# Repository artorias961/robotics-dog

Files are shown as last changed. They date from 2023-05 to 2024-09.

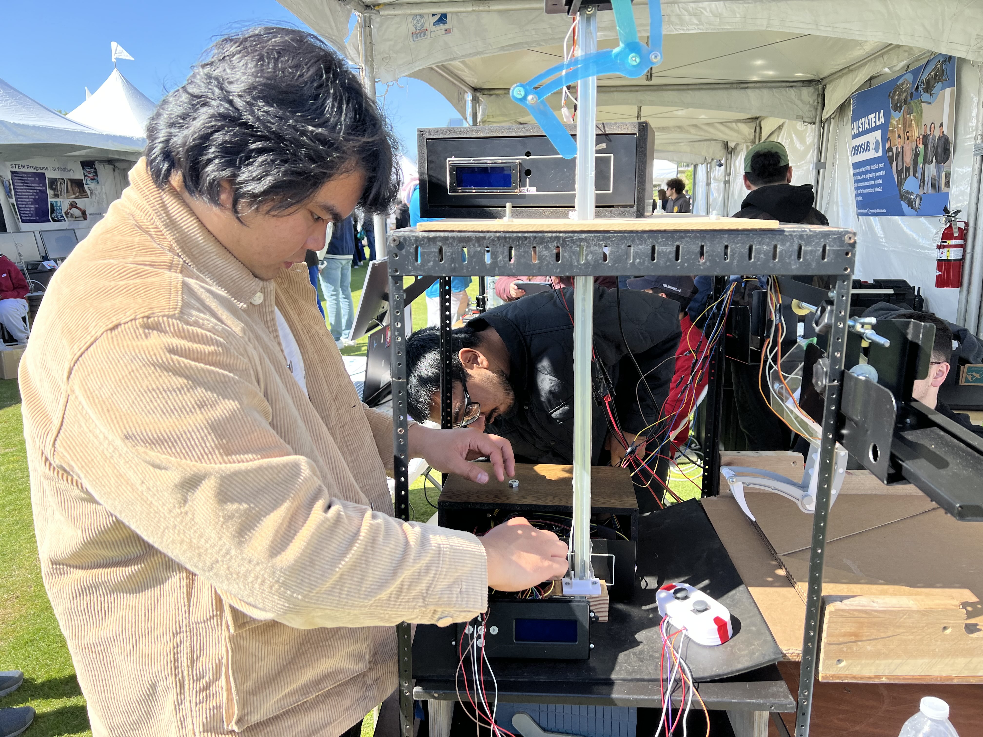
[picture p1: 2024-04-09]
events_photos/Spring_2024_Maker_Faire_Downtown_LA/IMG_5998.jpg

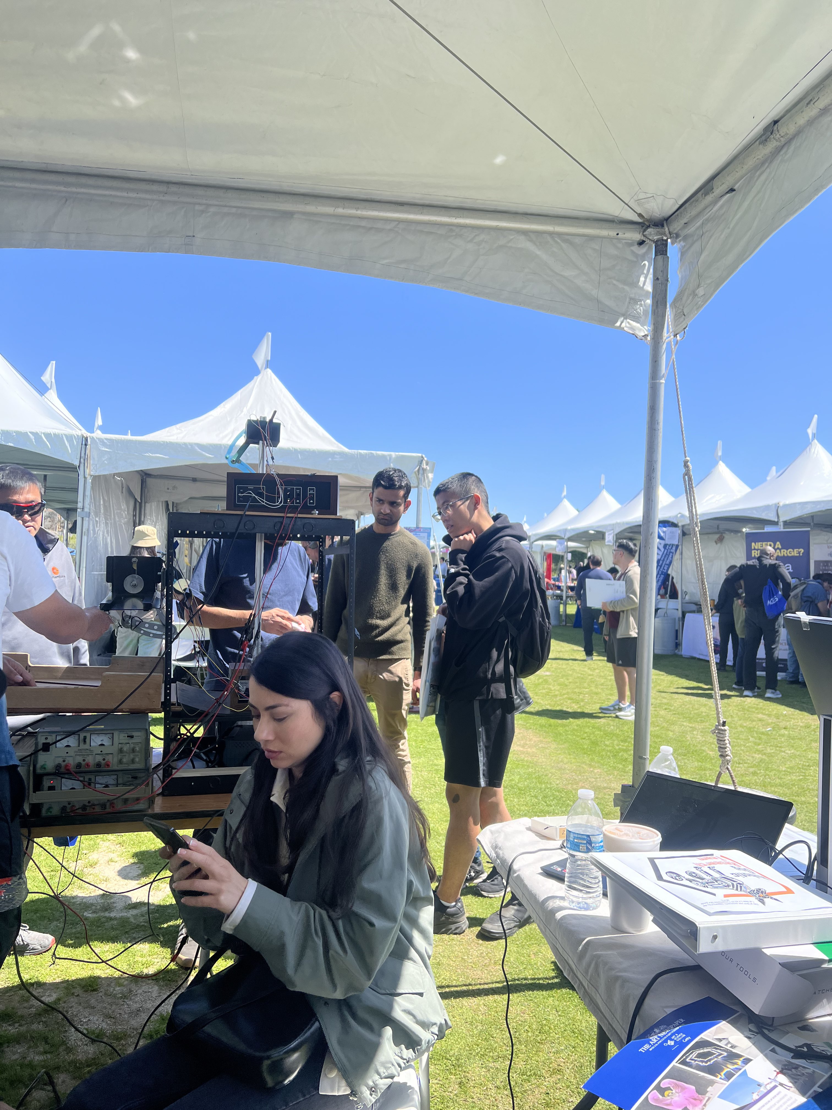
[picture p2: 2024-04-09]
events_photos/Spring_2024_Maker_Faire_Downtown_LA/IMG_3934.jpg

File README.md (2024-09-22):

# Idea of the Project

This project aims to develop a guided tour robot designed to assist individuals with disabilities in navigating the California State University, Los Angeles campus. The robot will utilize detailed floor plans of campus buildings and follow a pre-set route. It will be equipped with advanced computer vision technology to detect and avoid obstacles, enhancing safe navigation. Key features include:

1. **Diverse Sensor Array**: The robot will employ a variety of sensors like LiDAR, ultrasonic sensors, cameras, IR proximity sensors, and a GPS module. These tools will gather essential data about the environment, aiding in the robot's localization and obstacle detection.

2. **Internal Monitoring Sensors**: Internally, the robot will have Inertial Measurement Units (IMUs), position sensors, load sensors, and current sensors. These will monitor the robot's status and ensure smooth operation.

3. **Microcontroller and Processor Integration**: The gathered sensor data will be processed by microcontrollers, which in turn feed into a central microprocessor. This setup allows for efficient data handling and control.

4. **Operating System and Control Software**: Ubuntu will be the operating system to manage high-level algorithms. The control software programmed into the system will execute precise commands, directing the robot's movements.

5. **Actuation System**: The robot's movement will be controlled by various motors, including servo, stepper, and brushless motors. This setup ensures a wide range of motion and adaptability to different terrains.

6. **Power Management**: Electronic subsystems will be implemented to power the motors and regulate the overall power supply, ensuring consistent and efficient energy usage.

7. **Structural Design**: The robot's exterior will primarily consist of 3D-printed components, supported by a robust, load-bearing internal frame. This design ensures durability while remaining lightweight for ease of maneuverability.

This tour robot is specially designed to make the Cal State LA campus more accessible to people with disabilities, offering a reliable and safe way to explore and navigate the university's facilities.

# Our Sponsors

This project has been graciously supported by ***IT Faculty Sergio Marquez from Cal State LA***, ***Cal State LA ECST CircuitSpace IRA Funds IR472***, ***Biomedical Engineering Society***, and ***MATHEMATICS, ENGINEERING SCIENCE ACHIEVEMENT (MESA)*** whose generous contributions have been instrumental in bringing our vision to life. 

We would also like to extend our deepest gratitude to the faculties at Cal State LA, Electrical Engineering Department. Their invaluable guidance, expertise, and unwavering support have been pivotal to the success of our project. The collaboration and insights provided by these dedicated professionals have greatly enriched our journey and contributed significantly to achieving our goals

# Early Contributors
We would like to acknowledge the key individuals who played an essential role in the early stages of this project. Special recognition goes to [Christopher Morales](https://christopher-morales.vercel.app) (EE graduate student) and **Anthony Perez** (ME undergraduate student), who were the primary initiators of the project. Beginning in January 2023 with the development of a robotic dog, their vision and hard work set the foundation for what would become a vital innovation in campus accessibility.

During the summer of 2023, the team expanded from 2 to 4 members, and by December, it had grown to 11 members. Some of these contributors graduated in the winter of 2023, but their impact on the project endures. This project holds a special place for Christopher Morales, who is excited to see it continue and thrive, even as of August 2024, when the project has grown and advanced without his direct involvement!

We also extend our gratitude to **Sergio Marquez** (Faculty) and **Dr. Wang** (Professor) for their invaluable guidance and support throughout the project's development. Together, their collective efforts have driven this project forward. A special thanks to **Sergio Marquez** for dedicating his own time and money to the project, even during the early stages when we had little to show, demonstrating his unwavering belief in our vision.

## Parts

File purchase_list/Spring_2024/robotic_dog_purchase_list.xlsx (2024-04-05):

Line Item | Priority | Item | Pkg. Qty | Pkg. Price | Order Qty | Tax | Shipping | Item Total | Notes | Distributor | Hazardous | ASIN | Link
1 | A | LattePanda Sigma - x86 Windows / Linux Single Board Computer Server (32GB RAM, 500GB, WiFi 6E) | 1 | $718.99 | 1 | $73.70 |  | $792.69 | Embedded Board | Amazon | N |  | https://www.amazon.com/LattePanda-Sigma-Windows-Single-Computer/dp/B0CKRLNBZF/?th=1
2 | A | LiperiAir 9500mAh 4S 100C 14.8V Lipo Battery With EC5 Plug for RC Plane / Car / Boat / Drone | 1 | $92.99 | 2 | $19.06 |  | $205.04 | Batteries | RCBatteries | Y |  | https://rcbattery.com/liperiair-9500mah-4s-100c-14-8v-lipo-battery-with-ec5-plug.html
 |  |  |  | The Grand Total: |  |  |  | $997.73

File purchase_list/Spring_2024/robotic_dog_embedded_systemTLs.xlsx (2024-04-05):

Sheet: Main Trade Analysis
Line Item | Priority | Item | Pkg. Qty | Pkg. Price | Order Qty | Tax | Shipping | Item Total | Notes | Distributor | Hazardous | ASIN | Link
1 | A | MINISFORUM AR900i ITX Motherboard | 1 | $539.99 | 1 | $55.35 |  | $595.34 | Embedded Board | Amazon | N | B0CTTMY5BW | https://www.amazon.com/MINISFORUM-Motherboard-i9-13900HX-Chipset-PCIe4-0/dp/B0CTTMY5BW
2 | A | Kingston NV2 1TB M.2 2280 | 1 | $60.99 | 1 | $6.25 |  | $67.24 | NVMe | Amazon | N | B0BBWH1R8H | https://www.amazon.com/Kingston-2280-Internal-SNV2S-1000G/dp/B0BBWH1R8H?s=electronics
3 | A | Crucial RAM 32GB Kit | 1 | $98.50 | 1 | $10.10 |  | $108.60 | SODIMM RAM | Amazon | N | ‎B0BLTDRRLF | https://www.amazon.com/Crucial-5600MHz-5200MHz-4800MHz-CT2K16G56C46S5/dp/B0BLTDRRLF?s=electronics
4 | A | Thermaltake Smart 500W 80+ White | 1 | $39.95 | 1 | $4.09 |  | $44.04 | PSU | Amazon | N | B014W3EM2W | https://www.amazon.com/Thermaltake-Certified-Continuous-cooling-PS-SPD-0500NPCWUS-W/dp/B014W3EM2W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
5 | A | Noctua NF-F12 PWM Fan | 1 | $21.78 | 1 | $2.23 |  | $24.01 | PWM Fan | Amazon | N | B00650P2ZC | https://www.amazon.com/Noctua-NF-F12-PWM-4-Pin-Premium/dp/B00650P2ZC?s=electronics
6 | A | LiperiAir 9500mAh 4S 100C 14.8V Lipo Battery | 1 | $93.00 | 1 | $9.53 |  | $102.53 | Battery | RC Battery.com | Y | LPL95004S100-E | https://rcbattery.com/liperiair-9500mah-4s-100c-14-8v-lipo-battery-with-ec5-plug.html
7 | A | Samlex America, IDC-200A-12, Switching DC-DC Converter | 1 | $188.60 | 1 | $19.33 |  | $207.93 | Power Electronics | Samlex Power | N | 622988067204 | https://www.invertersupply.com/index.php?main_page=product_info&products_id=2042
8 | A | PicoPSU-160-XT, 160w output, 12v input DC-DC Power Supply | 1 | $45.60 | 1 | $4.67 |  | $50.27 | Charger | Mini-Box.com | N | picoPSU-160-XT | https://www.mini-box.com/picoPSU-160-XT
 |  |  |  | The Grand Total: | 8 |  |  | $1199.97

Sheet: Power Calculations
Power calculations |  |  | https://www.batteryspace.com/ |  |  |  | https://rcbattery.com/
AR900i (https://www.amazon.com/MINISFORUM-Motherboard-i9-13900HX-Chipset-PCIe4-0/dp/B0CTTMY5BW) | DCDC converter |  |  |  |  |  |  |  | Weight
MB watts | efficents | Efecctive watts | voltage | run time hrs' | current | Amp*Hrs | Battery | Price | lbs | Link
100 | 0.85 | 115 | 12 | 1 | 9.583333333 | 9.583333333 | LiFePO4 26650 Battery: 12.8V 9.9Ah (126Wh, 30A rate, 26650-3300) $181.5 2.5lbs (https://www.batteryspace.com/custom-lfp-26650-battery-12-8v-9-9ah-126wh-30a-rate-with-pcb-in-special-configuration.aspx)
 |  |  |  |  |  |  | Liperior 22000mAh 4S 12C 14.8V Lipo Battery With XT90 Plug for RC Drone | $205.99 | 3.75 | https://rcbattery.com/liperior-22000mah-4s-12c-14-8v-lipo-battery-with-xt90-plug.html
 |  | 100 |  |  |  |  | Smart Charger (10A) for 12.8V LiFePO4 old $79.95 (https://www.batteryspace.com/Smart-Charger-10A-for-12.8V-LiFePO4-Rechargeable-Battery-Pack.aspx)
 |  | 1 | 0.85 |  |  |  | Lithium Polymer (Lipo) Fire Retardant Charger Bag | $4.49 |  | https://rcbattery.com/lithium-polymer-lipo-fire-retardant-bag-230mm-x-300mm.html
 |  |  |  |  |  |  | Ultra Power UP9, 200W, Four Channels Smart Balance Charger | $99.99 |  | https://rcbattery.com/ultra-power-up9-200w-four-channels-smart-balance-charger-ac-100w-dc-200w-us-plug.html
 |  |  |  |  |  |  | DCDC convert for 24 pin MB power plug 160W | $46.50 | 0.21 | https://www.mini-box.com/picoPSU-160-XT
 |  |  |  | 14.8 | 1.4 | 13.4 | requires 12V regulated max 13-13.5V | $60.99
 |  |  |  | 22 | 12 | 264 |  | $98.50
 |  |  |  |  |  |  |  | $39.95
 |  |  |  |  |  |  |  | $21.78
 |  |  |  |  |  |  | MINISFORUM AR900i Motherboard | $539.99 | 2.9 | https://www.amazon.com/MINISFORUM-Motherboard-i9-13900HX-Chipset-PCIe4-0/dp/B0CTTMY5BW
 |  |  |  |  |  |  | Regular DC-DC converter 12 volt out 200W | $188.60 | 1.4 | https://samlexamerica.com/wp-content/uploads/2020/01/11004-IDC-200-0417_Hrez.pdf
 |  |  |  |  |  |  |  | $1306.78 | 8.26

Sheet: in
Line Item | Priority | Item | Pkg. Qty | Pkg. Price | Order Qty | Tax | Shipping | Item Total | Notes | Distributor | Hazardous | ASIN | Link
1 | A | MINISFORUM AR900i ITX Motherboard | 1 | $539.99 | 1 | $55.35 |  | $595.34 | Embedded Board | Amazon | N | B0CTTMY5BW | https://www.amazon.com/MINISFORUM-Motherboard-i9-13900HX-Chipset-PCIe4-0/dp/B0CTTMY5BW
2 | A | Kingston NV2 1TB M.2 2280 | 1 | $60.99 | 1 | $6.25 |  | $67.24 | NVMe | Amazon | N | B0BBWH1R8H | https://www.amazon.com/Kingston-2280-Internal-SNV2S-1000G/dp/B0BBWH1R8H?s=electronics
3 | A | Crucial RAM 32GB Kit | 1 | $98.50 | 1 | $10.10 |  | $108.60 | SODIMM RAM | Amazon | N | ‎B0BLTDRRLF | https://www.amazon.com/Crucial-5600MHz-5200MHz-4800MHz-CT2K16G56C46S5/dp/B0BLTDRRLF?s=electronics
4 | A | Thermaltake Smart 500W 80+ White | 1 | $39.95 | 1 | $4.09 |  | $44.04 | PSU | Amazon | N | B014W3EM2W | https://www.amazon.com/Thermaltake-Certified-Continuous-cooling-PS-SPD-0500NPCWUS-W/dp/B014W3EM2W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
5 | A | Noctua NF-F12 PWM Fan | 1 | $21.78 | 1 | $2.23 |  | $24.01 | PWM Fan | Amazon | N | B00650P2ZC | https://www.amazon.com/Noctua-NF-F12-PWM-4-Pin-Premium/dp/B00650P2ZC?s=electronics
6 | B | Regular DC-DC converter 12 volt out 200W | 1 | $188.60 | 1 | $19.33 |  | $207.93 | Power Electronics | Samlex Power | N | / | 11004-IDC-200-0417_Hrez.pdf (samlexamerica.com) (https://samlexamerica.com/wp-content/uploads/2020/01/11004-IDC-200-0417_Hrez.pdf)
7 | B | HRB 14.8V 4S LiPO Battery 9500mAh 120C (sale) | 1 | $88.30 | 1 | $9.05 |  | $97.35 | Battery | HRB-Power | N | / | https://hrb-power.com/products/hrb-14-8v-4s-lipo-battery-9500mah-120c-for-rc-car-x-maxx-v2-udr-car-truck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
8 | A | LiperiAir 9500mAh 4S 100C 14.8V Lipo Battery | 1 | $93.00 | 1 | $9.53 |  | $102.53 | Battery | RC Battery.com | N | LPL95004S100-E | https://rcbattery.com/liperiair-9500mah-4s-100c-14-8v-lipo-battery-with-ec5-plug.html
 | B | CNHL Racing Series 9500mAh 14.8V 4S 90C LiPo (EC5) | 1 | $91.90 | 1 | $9.42 |  | $101.32 | Battery | Classicrcshop.com | N | 950904EC5 | https://classicrcshop.com/products/cnhl-racing-series-9500mah-14-8v-4s-90c-lipo-battery-with-ec5-plug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
10 | A | 12V DIN Rail DC/DC Converter 99.6 Watts | 1 | $67.30 | 1 | $6.90 |  | $74.20 | DC converter | TRC Electronics | N | EN50155 | https://trcelectronics.com/products/mean-well-ddr-120a-12?_pos=1&_sid=1fe48ef6a&_ss=r&_fid=a136a3afc
11 | A | DC-DC Converter, Half Brick, 200 Watt, 4:1 Input Range, 10-36V Input Voltage, 12VDC Output | 1 | $161.81 | 1 | $16.59 |  | $178.40 | DC converter | Mouser | N | 418-CHB200W-24S12 | https://www.mouser.com/ProductDetail/Cincon/CHB200W-24S12
12 | A | DCDC convert for 24 pin MB power plug 160W | 1 | $45.60 | 1 | $4.67 |  | $50.27 | Charger | Mini-Box.com | N | picoPSU-160-XT | https://www.mini-box.com/picoPSU-160-XT
13 | A | Ultra Power UP9, 200W, Four Channels Smart Balance Charger | 1 | $100.00 | 1 | $10.25 |  | $110.25 | SmartCharger | RC Battery.com | N | / | https://rcbattery.com/ultra-power-up9-200w-four-channels-smart-balance-charger-ac-100w-dc-200w-us-plug.html
14 | B | Lithium Polymer (Lipo) Fire Retardant Charger Bag | 1 | $4.50 | 1 | $0.46 |  | $4.96 | Bag | RC Battery.com | N | RCB00001 | https://rcbattery.com/lithium-polymer-lipo-fire-retardant-bag-230mm-x-300mm.html
15 | B | Liperior 22000mAh 4S 12C 14.8V Lipo Battery With XT90 Plug for RC Drone | 1 | $206.00 | 1 | $21.11 |  | $227.12 | Battery | RC Battery.com | N | LP220004S12 | https://rcbattery.com/liperior-22000mah-4s-12c-14-8v-lipo-battery-with-xt90-plug.html
16 | B | Smart Charger (10A) for 12.8V LiFePO4 | 1 | $80.00 | 1 | $8.20 |  | $88.20 | Smart charger | batteryspace.com | N | / | https://www.batteryspace.com/Smart-Charger-10A-for-12.8V-LiFePO4-Rechargeable-Battery-Pack.aspx
 |  |  |  | The Grand Total: | 16 |  |  | $2081.76

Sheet: Power Calculations (2)
Power calculations |  |  | https://www.batteryspace.com/ |  |  |  | https://rcbattery.com/
AR900i (https://www.amazon.com/MINISFORUM-Motherboard-i9-13900HX-Chipset-PCIe4-0/dp/B0CTTMY5BW) | DCDC converter |  |  |  |  |  |  |  | Weight
MB watts | efficents | Efecctive watts | voltage | run time hrs' | current | Amp*Hrs | Battery | Price | lbs | Link
100 | 0.85 | 115 | 12 | 1 | 9.583333333 | 9.583333333 | LiFePO4 26650 Battery: 12.8V 9.9Ah (126Wh, 30A rate, 26650-3300) $181.5 2.5lbs (https://www.batteryspace.com/custom-lfp-26650-battery-12-8v-9-9ah-126wh-30a-rate-with-pcb-in-special-configuration.aspx)
 |  |  |  |  |  |  | Liperior 22000mAh 4S 12C 14.8V Lipo Battery With XT90 Plug for RC Drone | $205.99 | 3.75 | https://rcbattery.com/liperior-22000mah-4s-12c-14-8v-lipo-battery-with-xt90-plug.html
 |  | 100 |  |  |  |  | Smart Charger (10A) for 12.8V LiFePO4 old $79.95 (https://www.batteryspace.com/Smart-Charger-10A-for-12.8V-LiFePO4-Rechargeable-Battery-Pack.aspx)
 |  | 1 | 0.85 |  |  |  | Lithium Polymer (Lipo) Fire Retardant Charger Bag | $4.49 |  | https://rcbattery.com/lithium-polymer-lipo-fire-retardant-bag-230mm-x-300mm.html
 |  |  |  |  |  |  | Ultra Power UP9, 200W, Four Channels Smart Balance Charger | $99.99 |  | https://rcbattery.com/ultra-power-up9-200w-four-channels-smart-balance-charger-ac-100w-dc-200w-us-plug.html
 |  |  |  |  |  |  | DCDC convert for 24 pin MB power plug 160W | $46.50 | 0.21 | https://www.mini-box.com/picoPSU-160-XT
 |  |  |  | 14.8 | 1.4 | 13.4 | requires 12V regulated max 13-13.5V | $60.99
 |  |  |  | 22 | 12 | 264 |  | $98.50
 |  |  |  |  |  |  |  | $39.95
 |  |  |  |  |  |  |  | $21.78
 |  |  |  |  |  |  | MINISFORUM AR900i Motherboard | $539.99 | 2.9 | https://www.amazon.com/MINISFORUM-Motherboard-i9-13900HX-Chipset-PCIe4-0/dp/B0CTTMY5BW
 |  |  |  |  |  |  | Regular DC-DC converter 12 volt out 200W | $188.60 | 1.4 | https://samlexamerica.com/wp-content/uploads/2020/01/11004-IDC-200-0417_Hrez.pdf
 |  |  |  |  |  |  |  | $1306.78 | 8.26
 |  |  |  |  |  | Other DC-DC converters
 |  |  |  |  |  |  | DC-DC Converter, Half Brick, 200 Watt, 4:1 Input Range, 10-36V Input Voltage, 12VDC Output | $161.81 | 0.25 | https://www.mouser.com/ProductDetail/Cincon/CHB200W-24S12
 |  |  |  |  |  |  | 12V DIN Rail DC/DC Converter 99.6 Watts | $67.30 | 2.2 | https://trcelectronics.com/products/mean-well-ddr-120a-12?_pos=1&_sid=1fe48ef6a&_ss=r&_fid=a136a3afc
 |  |  |  |  |  | Smaller Batteries
 |  |  |  |  |  |  | CNHL Racing Series 9500mAh 14.8V 4S 90C LiPo (EC5) | $91.99 | 1.7 | https://classicrcshop.com/products/cnhl-racing-series-9500mah-14-8v-4s-90c-lipo-battery-with-ec5-plug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
 |  |  |  |  |  |  | LiperiAir 9500mAh 4S 100C 14.8V Lipo Battery | $92.99 | 1.71 | https://rcbattery.com/liperiair-9500mah-4s-100c-14-8v-lipo-battery-with-ec5-plug.html
 |  |  |  |  |  |  | HRB 14.8V 4S LiPO Battery 9500mAh 120C (sale) | $88.30 | 1.69 | https://hrb-power.com/products/hrb-14-8v-4s-lipo-battery-9500mah-120c-for-rc-car-x-maxx-v2-udr-car-truck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

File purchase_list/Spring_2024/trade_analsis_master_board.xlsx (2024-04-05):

Trade Analysis for Master Board
Name of Board | LattePanda Sigma (https://www.dfrobot.com/product-2720.html) | AsRock Industrial Board (https://www.newegg.com/asrock-industrial-4x4-box-7735u/p/N82E16856179002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) | NVIDIA Jetson Orin Nano (https://www.digikey.com/en/products/detail/seeed-technology-co-ltd/102110839/19285410) | Kria KR260 Starter Kit (https://www.digikey.com/en/products/detail/amd/SK-KR260-G/16521660)
Processor | i5-1340P (12 core) x86 | 5 7535U (6 core) x86 | Cortex A78E (12 Core) Arm | Mutliple Cortex (6 cpus) Arm
Memory | 32 GB (LPDDR5) | 0 GB (DDR5) | 8 GB (LPDDR5) | 4 GB (System on Module)
Graphics | Intel Iris Xe Graphics | Integrated Graphics | Integrated Graphics | Integrated Graphics
Storage | 0 GB (M.2 NMVe/Sata) | 0GB (2x M.2.) | 0 GB (NVMe) | 0 GB (Micro SD)
Cooling | On board Fan | No Fan | On Board Fan | On Board Fan
ROS Version | ROS 1 and ROS 2 (https://docs.lattepanda.com/content/sigma_edition/Operating_Systems/) | ROS 1 and ROS 2 | ROS 1 | ROS 2
Operating System | Windows 10/11, Ubuntu 20/22 | Windows 10/11 | Ubuntu 20.04 | Ubuntu 22.04 LTS
Size | 146mm x 102mm | 104mmx36mm102mm | 70mmx45mm | 119mmx140mmx36mm
Price | $629.00 | $500.00 | $598.80 | $397.86
Power In | 12V-20V | 12V-24V | 5V-20V | 12V
Ports | (3) M.2 NVMe/SATA, (4) USB, (2) type c thunderbolt, header pins, Micro SIM Card, (1) HDMI 2.1, (2) 2.5 GB RJ45 Ethernet, (1) DP | HDMI 2.1, (3) DP 1.4A, (2)Ethernet [2.5GbE and GbE LAN], (5) USB Port | micro SD, Type C, header pin, (3) M.2, DP | (4) RJ45, (4) USB, Micro SD, (4) PMOD, DP

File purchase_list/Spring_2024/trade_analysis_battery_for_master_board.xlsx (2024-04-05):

Battery Trade Analysis for Master Board
Name of Battery | LiperiAir 9500 mAh 4S 100C 14.8V Lipo Battery (https://rcbattery.com/liperiair-9500mah-4s-100c-14-8v-lipo-battery-with-ec5-plug.html) | CNHL 4s lipo Battery 9500mAh 14.8V 90C lipo Battery (https://www.amazon.com/CNHL-Battery-9500mAh-14-8V-Truck/dp/B0BRCCRQFC) | HRB 14.8V 4S LiPO Battery 9500mAh 120C (https://hrb-power.com/products/hrb-14-8v-4s-lipo-battery-9500mah-120c-for-rc-car-x-maxx-v2-udr-car-truck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) | Liperior 22000mAh 4S 12C 14.8V Lipo Battery With XT90 Plug for RC Drone (https://rcbattery.com/liperior-22000mah-4s-12c-14-8v-lipo-battery-with-xt90-plug.html)
Price | $92.99 | $165.99 | $88.30 | $205.99
Voltage Output (V) | 14.8 | 14.8 | 14.8 | 14.8
Discharge Rate (C) | 100 | 90 | 120 | 12
Capacity (mAh) | 9500 | 9500 | 9500 | 22000
Dimensions (l x w x h) | 175x41x50mm | 180.09x41.95x48.01mm | 166x51x42mm | 209x90x46mm
Weight (g) | 780 | 1090 | 771 | 1703
Density (Wh/kg) | 1897.44 | 1222.02 | 2303.50 | 104.29
Ports | EC5 | EC5 | EC5 + TRX | XT90
Package Quantity | 1 | 2 | 1 | 1
Quantity | 1 | 1 | 1 | 1
Cells | 4 | 4 | 4 | 4

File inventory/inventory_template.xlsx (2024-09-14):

Line Item | Priority | Item | Serial # | Location | Box Number | Tax | Shipping | Item Total | Notes | Distributor | Hazardous | ASIN | Link
1 | A
2 | B
3 | A
4 | C
5 | D
6
7
8
9
10
11
12
13
14
15
16
17
18
19
20
21
22
23
24
25
26
27
28
The Grand Total: |  |  |  |  |  | $0.00
Priority Levels
A | Urgent
B | High
C | Med
D | Low

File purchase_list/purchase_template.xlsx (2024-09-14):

Line Item | Priority | Item | Pkg. Qty | Pkg. Price | Order Qty | Tax | Shipping | Item Total | Notes | Distributor | Hazardous | ASIN | Link
1 | A |  | 1 | $0.00 | 0 | $0.00 | $0.00 | $0.00
2 | B |  | 1 | $0.00 | 0 | $0.00 | $0.00 | $0.00
3 | A |  | 1 | $0.00 | 0 | $0.00 | $0.00 | $0.00
4 | C |  | 1 | $0.00 | 0 | $0.00 | $0.00 | $0.00
5 | D |  | 1 | $0.00 | 0 | $0.00 | $0.00 | $0.00
6 |  |  | 1 | $0.00 | 0 | $0.00 | $0.00 | $0.00
7 |  |  | 1 | $0.00 | 0 | $0.00 | $0.00 | $0.00
8 |  |  | 1 | $0.00 | 0 | $0.00 | $0.00 | $0.00
9 |  |  | 1 | $0.00 | 0 | $0.00 | $0.00 | $0.00
10 |  |  | 1 | $0.00 | 0 | $0.00 | $0.00 | $0.00
11 |  |  | 1 | $0.00 | 0 | $0.00 | $0.00 | $0.00
12 |  |  | 1 | $0.00 | 0 | $0.00 | $0.00 | $0.00
13 |  |  | 1 | $0.00 | 0 | $0.00 | $0.00 | $0.00
14 |  |  | 1 | $0.00 | 0 | $0.00 | $0.00 | $0.00
15 |  |  | 1 | $0.00 | 0 | $0.00 | $0.00 | $0.00
16 |  |  | 1 | $0.00 | 0 | $0.00 | $0.00 | $0.00
17 |  |  | 1 | $0.00 | 0 | $0.00 | $0.00 | $0.00
18 |  |  | 1 | $0.00 | 0 | $0.00 | $0.00 | $0.00
19 |  |  | 1 | $0.00 | 0 | $0.00 | $0.00 | $0.00
20 |  |  | 1 | $0.00 | 0 | $0.00 | $0.00 | $0.00
21 |  |  | 1 | $0.00 | 0 | $0.00 | $0.00 | $0.00
22 |  |  | 1 | $0.00 | 0 | $0.00 | $0.00 | $0.00
23 |  |  | 1 | $0.00 | 0 | $0.00 | $0.00 | $0.00
24 |  |  | 1 | $0.00 | 0 | $0.00 | $0.00 | $0.00
25 |  |  | 1 | $0.00 | 0 | $0.00 | $0.00 | $0.00
26 |  |  | 1 | $0.00 | 0 | $0.00 | $0.00 | $0.00
27 |  |  | 1 | $0.00 | 0 | $0.00 | $0.00 | $0.00
28 |  |  | 1 | $0.00 | 0 | $0.00 | $0.00 | $0.00
The Grand Total: |  |  |  |  |  | $0.00
Priority Levels
A | Urgent
B | High
C | Med
D | Low

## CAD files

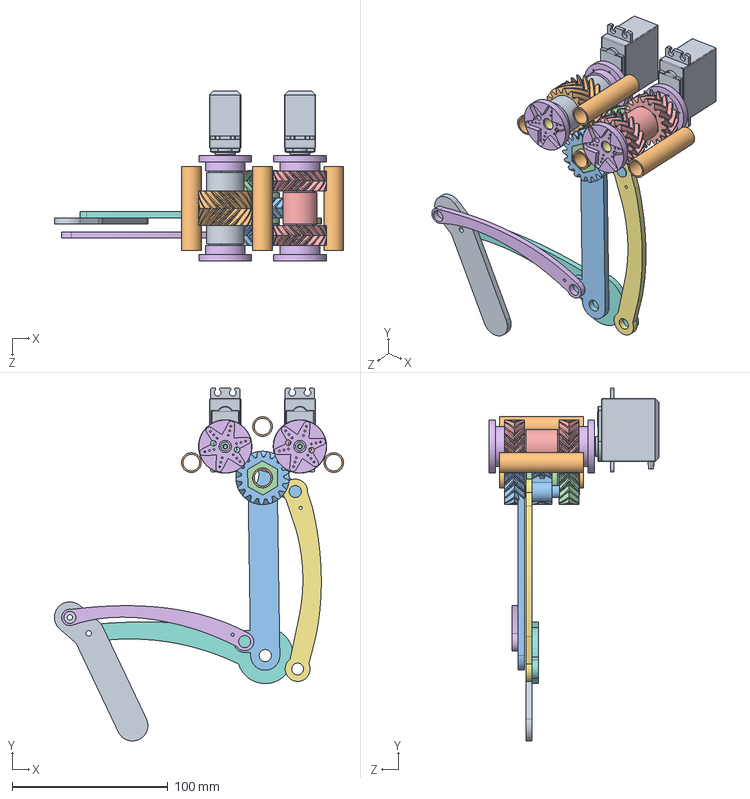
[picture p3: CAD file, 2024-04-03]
Rear_Dog1Leg/HipGearBoxv01v1.SLDASM
185.9 x 226.9 x 109.4 mm
MG995R Dogv00 x 2
GearAxelv01 x 4
QuadDHG001
HexShaft
HexShaftThighDrive
HornAdapterCap04 x 4
HornAdapterCapCuppler04 x 4
HexShaftQuadDrive
HexShaftQuadDriveSpacer x 2
DriveQuadDHG001
OuterThigh_DHG001
InnerThigh_DHG001
DHGSides001 x 2
RearCalf001
RearQuads001
RearShin001
RearFoot001

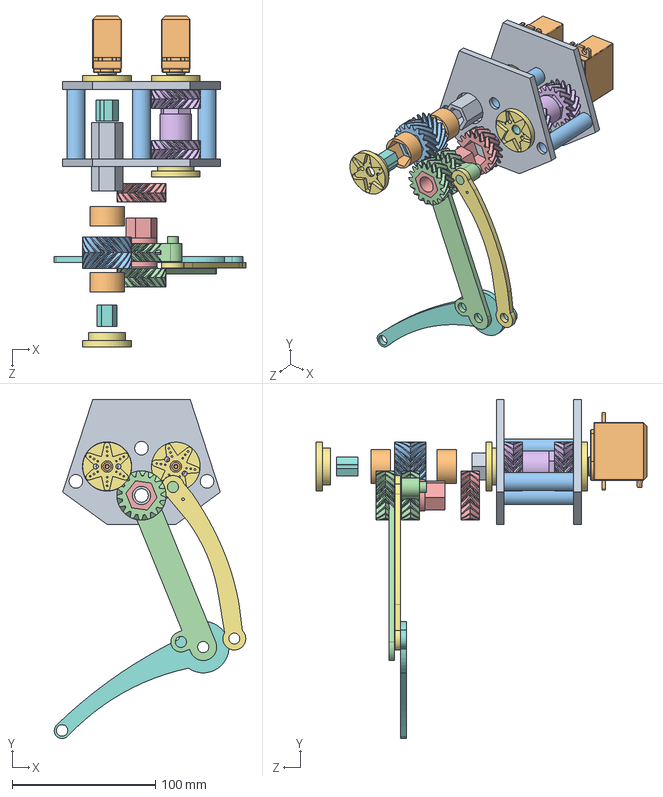
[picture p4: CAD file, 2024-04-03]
Rear_Dog1Leg/HipGearBoxv01.SLDASM
133.7 x 236.7 x 231.0 mm
GearBoxPlatev01 x 2
MG995R Dogv00 x 2
GearAxelv01 x 4
QuadDHG001
HexShaft
HexShaftThighDrive
HornAdapterCap04 x 4
HornAdapterCapCuppler04 x 4
HexShaftQuadDrive
HexShaftQuadDriveSpacer x 2
DriveQuadDHG001
OuterThigh_DHG001
InnerThigh_DHG001
DHGSides001 x 2
RearQuads001
RearShin001

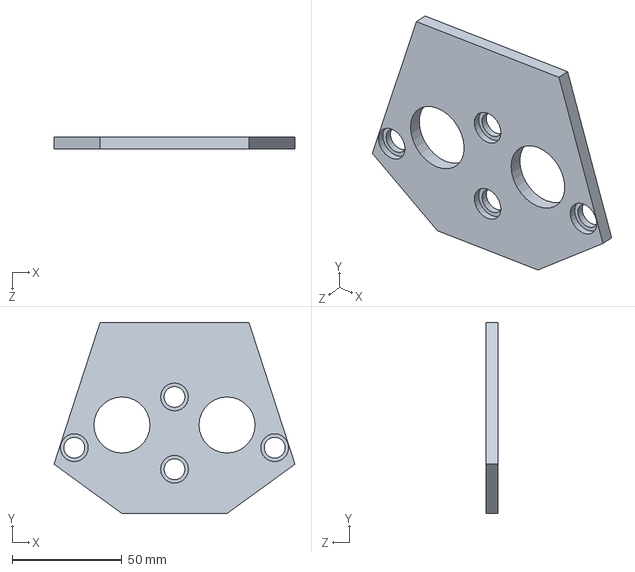
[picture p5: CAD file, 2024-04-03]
Rear_Dog1Leg/GearBoxPlatev01.SLDPRT
110.0 x 87.2 x 5.33 mm

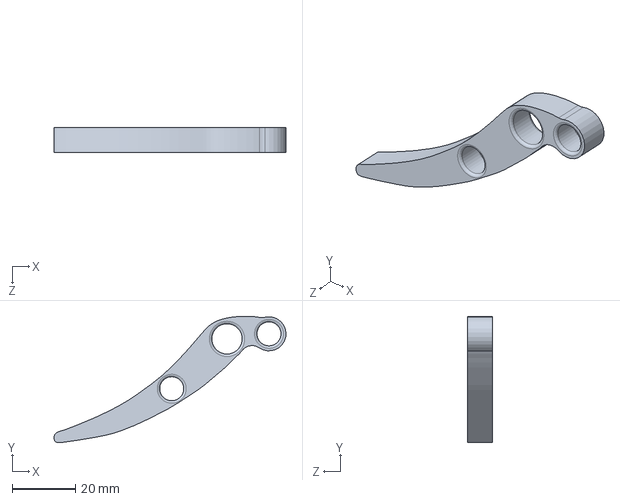
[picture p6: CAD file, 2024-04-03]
Rear_Dog1Leg/RearFootv02.SLDPRT
73.5 x 40.0 x 8.00 mm

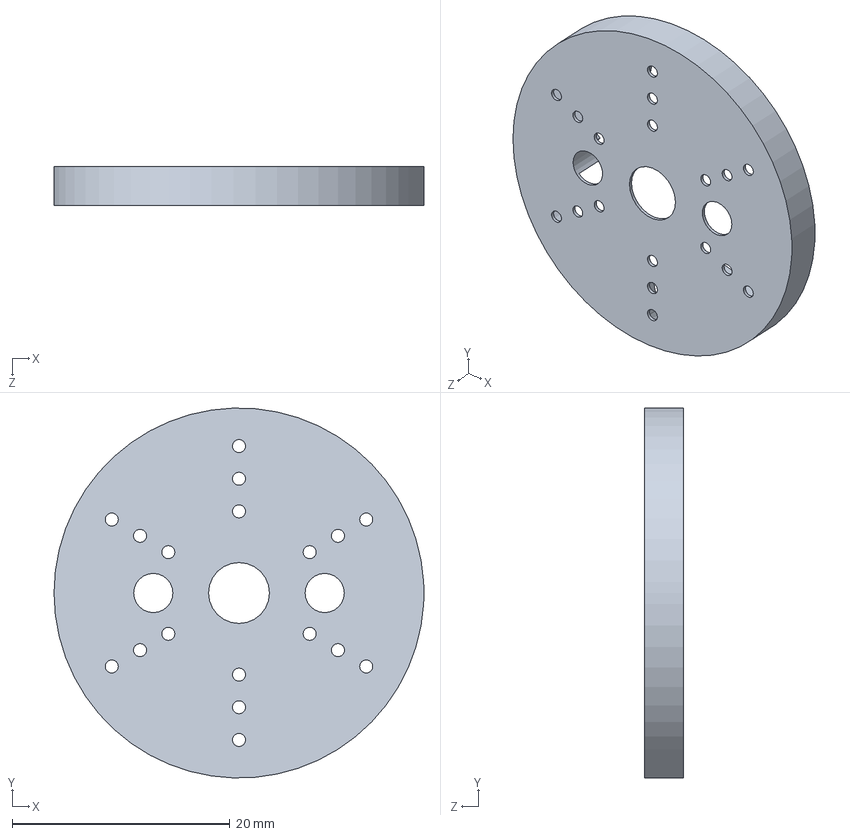
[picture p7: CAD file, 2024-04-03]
Rear_Dog1Leg/QuadHornAdapter01.SLDPRT
34.0 x 34.0 x 3.60 mm

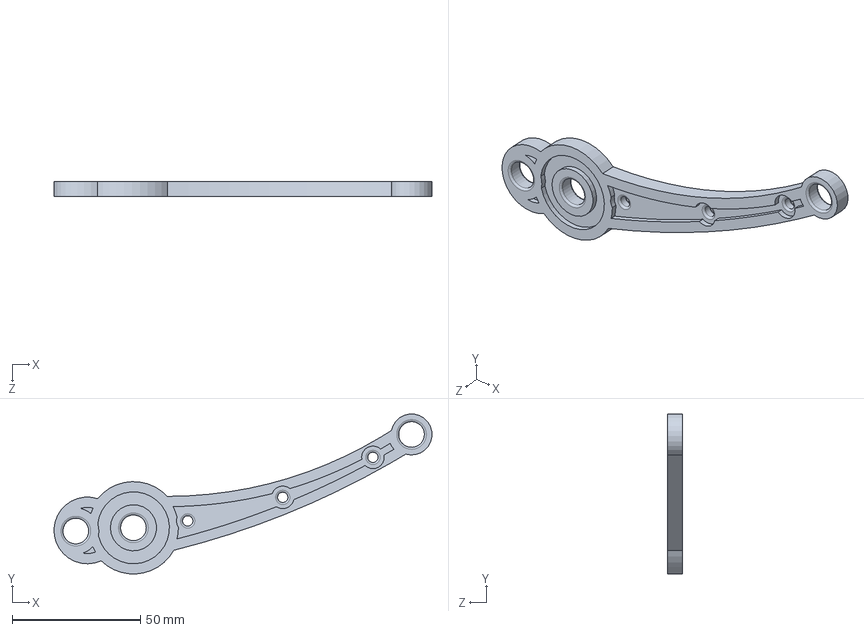
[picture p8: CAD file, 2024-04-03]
Rear_Dog1Leg/RearShinOuterv02.SLDPRT
147.4 x 62.3 x 6.00 mm

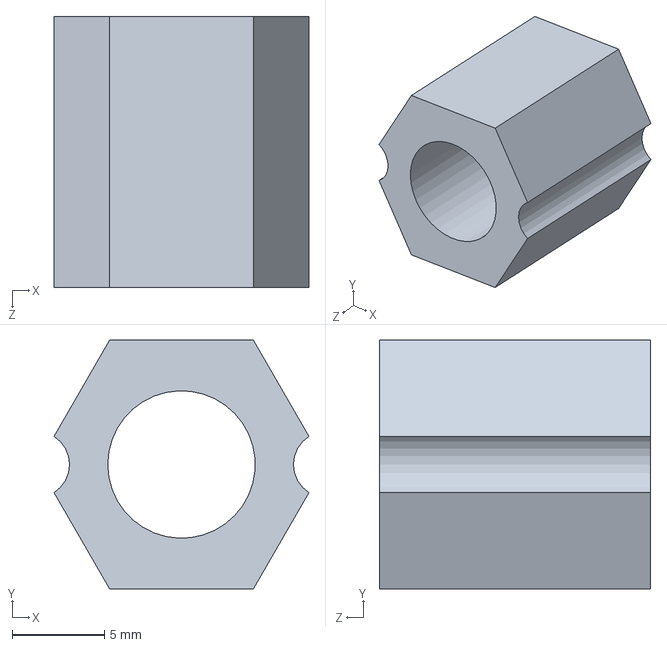
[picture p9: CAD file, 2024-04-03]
Rear_Dog1Leg/HornAdapterCapCuppler04.SLDPRT
13.8 x 13.5 x 14.7 mm

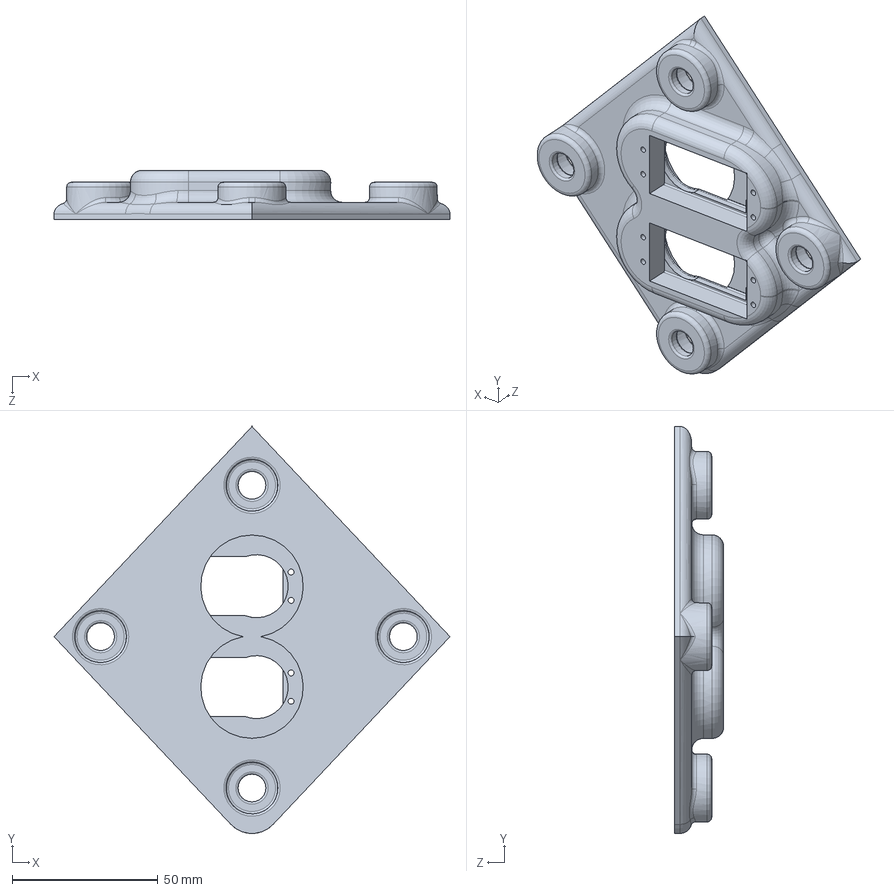
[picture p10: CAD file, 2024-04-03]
Rear_Dog1Leg/ServoMountv04.SLDPRT
136.1 x 139.9 x 17.0 mm

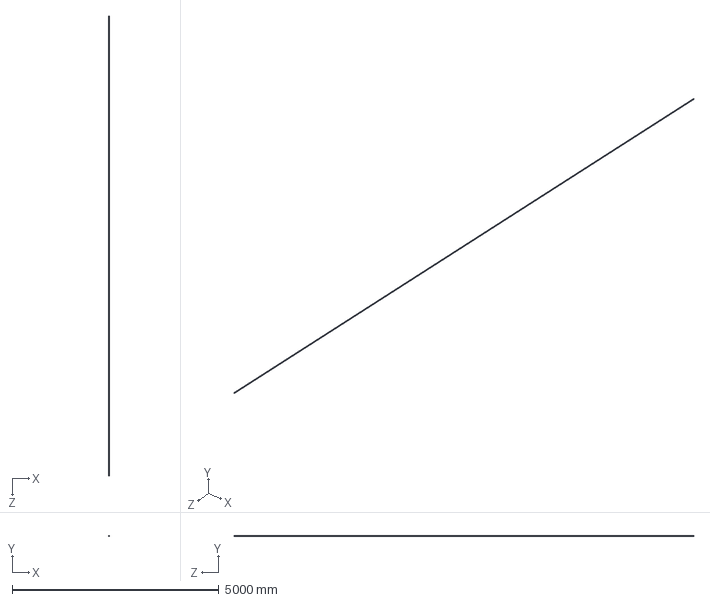
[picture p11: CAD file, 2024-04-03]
Rear_Dog1Leg/StainlessSteelTube38x05.SLDPRT
12.7 x 12.7 x 11125.2 mm

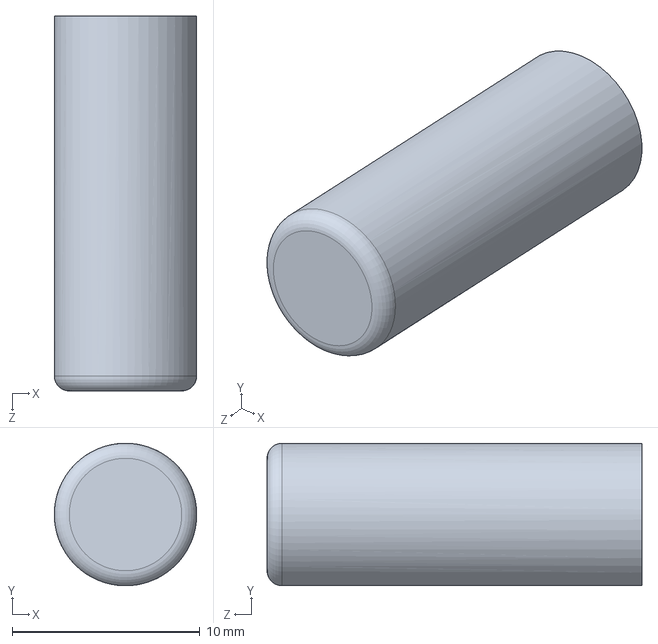
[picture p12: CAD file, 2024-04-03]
Rear_Dog1Leg/QuadQuadBridgev02.SLDPRT
7.60 x 7.60 x 20.0 mm

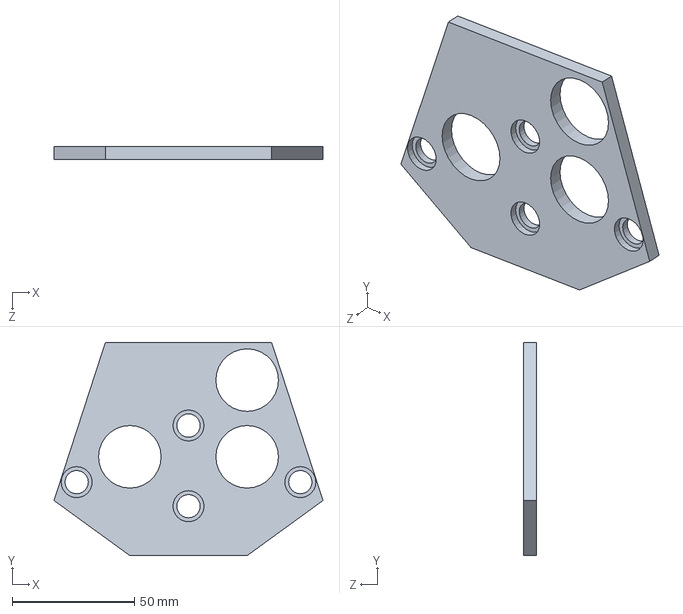
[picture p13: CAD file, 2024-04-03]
Rear_Dog1Leg/GearBoxFrontPlatev02.SLDPRT
110.0 x 87.2 x 5.33 mm

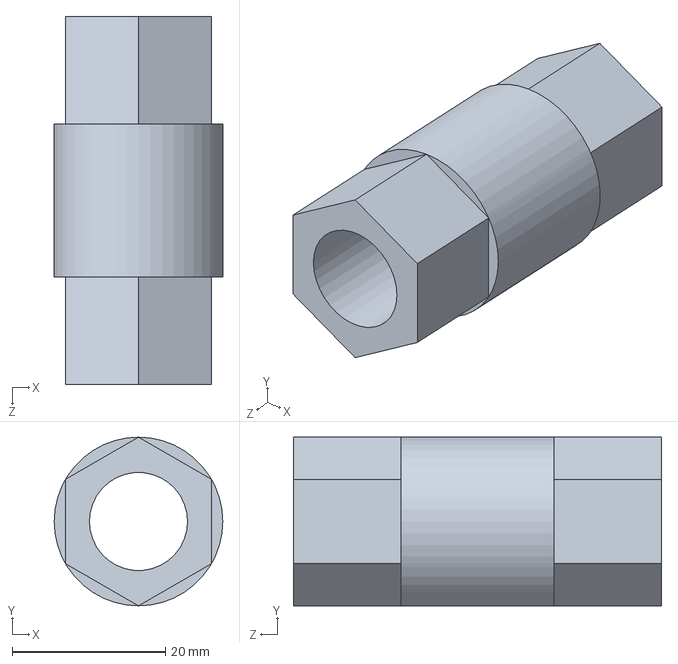
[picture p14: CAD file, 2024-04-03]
Rear_Dog1Leg/HexShaft.SLDPRT
22.0 x 22.0 x 48.0 mm

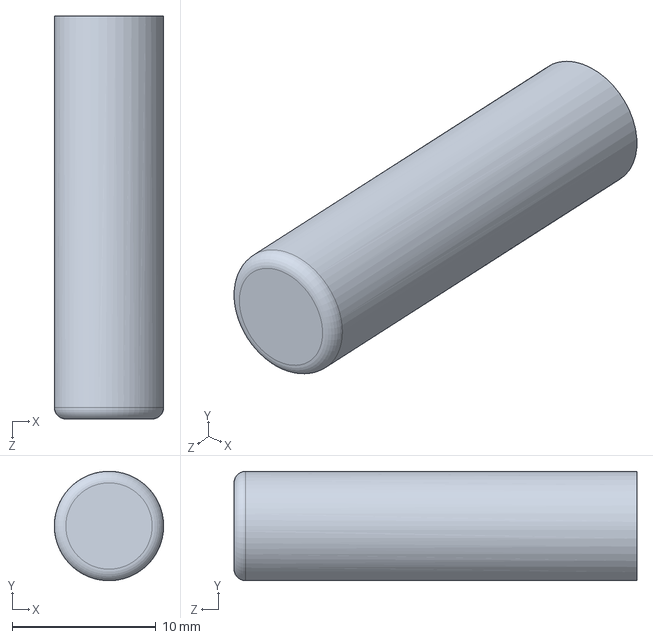
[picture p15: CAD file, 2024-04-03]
Rear_Dog1Leg/FootFootBridgev02.SLDPRT
7.60 x 7.59 x 28.0 mm

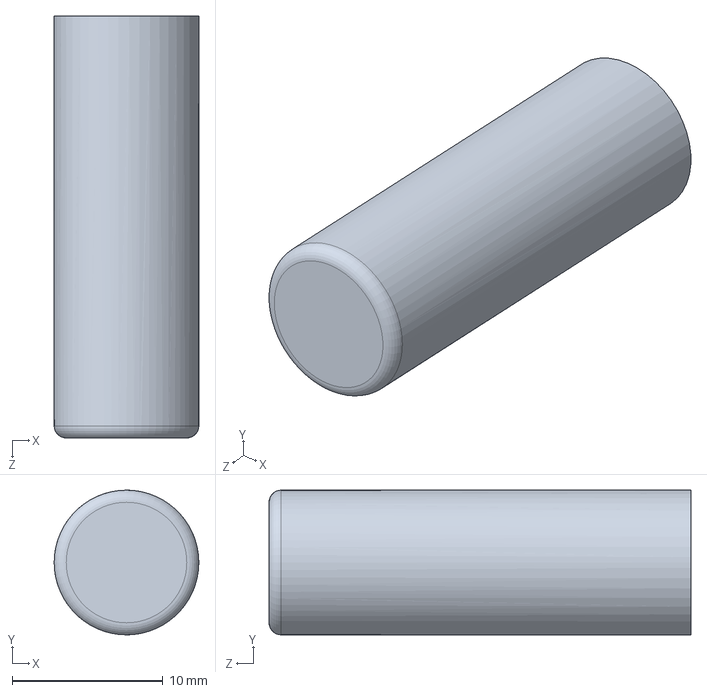
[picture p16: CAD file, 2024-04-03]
Rear_Dog1Leg/FootShinPivotv02.SLDPRT
9.60 x 9.60 x 28.0 mm

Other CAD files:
Rear_Dog1Leg/HornAdapterCap04.SLDPRT
Rear_Dog1Leg/HexShaftShoulderDrive_v0.2.SLDPRT
Rear_Dog1Leg/HexShaftThighDrive.SLDPRT
Rear_Dog1Leg/QuadShinPivotv02.SLDPRT
Rear_Dog1Leg/DoubleHelicalGear001.SLDPRT
Rear_Dog1Leg/FootCalfPivotv02.SLDPRT
Rear_Dog1Leg/GearAxelv01.SLDPRT
Rear_Dog1Leg/GearBoxBackPlatev02.SLDPRT
Rear_Dog1Leg/GearBoxPlatev02.SLDPRT
Rear_Dog1Leg/HexNut3_8-16.SLDPRT
Rear_Dog1Leg/HexShaftQuadDrive.SLDPRT
Rear_Dog1Leg/HexShaftQuadDriveSpacer.SLDPRT
Rear_Dog1Leg/HexShaftQuadDriveSpacerv02.SLDPRT
Rear_Dog1Leg/HexShaftThighDrivev02.SLDPRT
Rear_Dog1Leg/HexShaftv02.SLDPRT
Rear_Dog1Leg/HornAdapterCap01.SLDPRT
Rear_Dog1Leg/HornAdapterCap02.SLDPRT
Rear_Dog1Leg/HornAdapterCap03.SLDPRT
Rear_Dog1Leg/MG995R Dogv00.SLDPRT
Rear_Dog1Leg/MakerfairBooth.SLDPRT
Rear_Dog1Leg/MechaGodzilla.SLDPRT
Rear_Dog1Leg/PlasticSheet18x24x021.SLDPRT
Rear_Dog1Leg/RearCalf001.SLDPRT
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

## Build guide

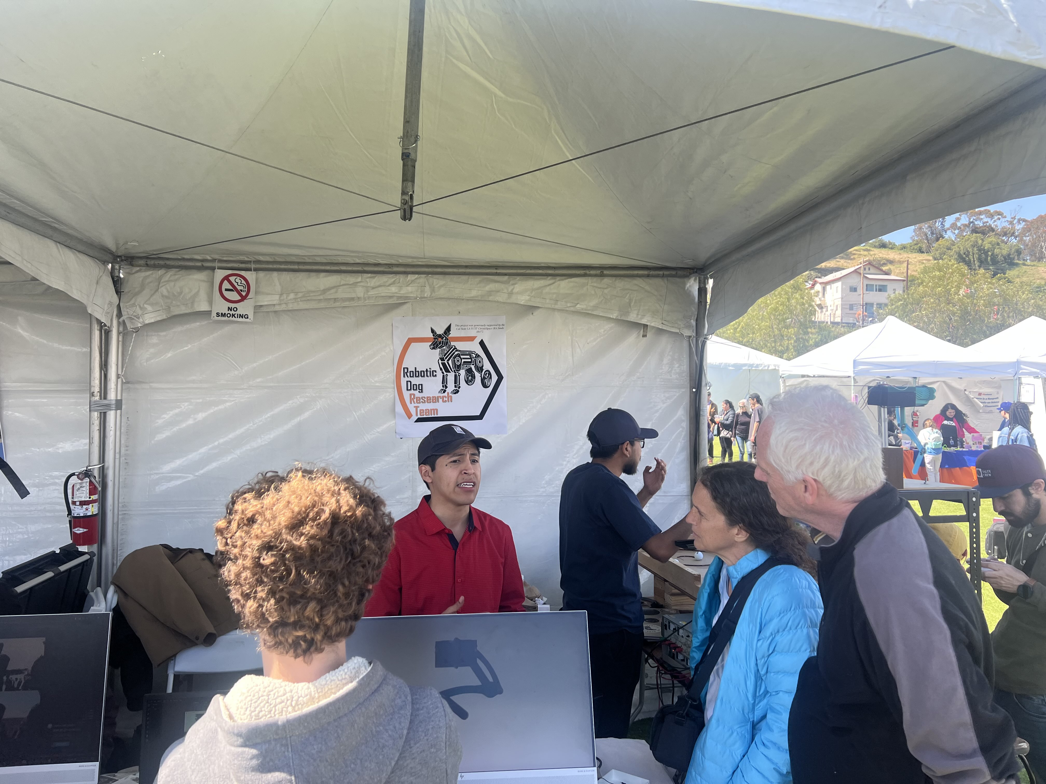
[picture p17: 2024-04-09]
events_photos/Spring_2024_Maker_Faire_Downtown_LA/IMG_6019.jpg

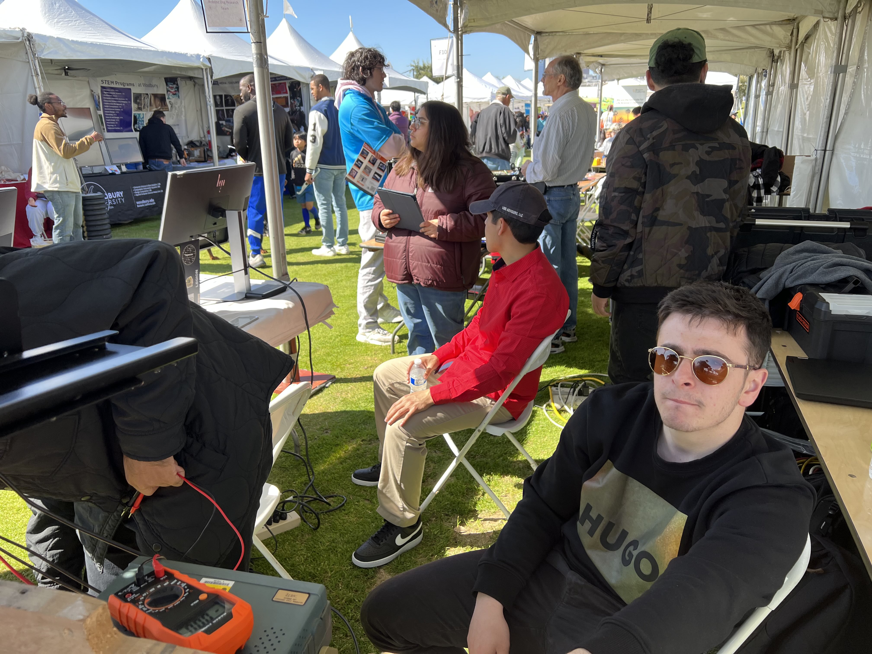
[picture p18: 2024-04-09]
events_photos/Spring_2024_Maker_Faire_Downtown_LA/IMG_5997.jpg

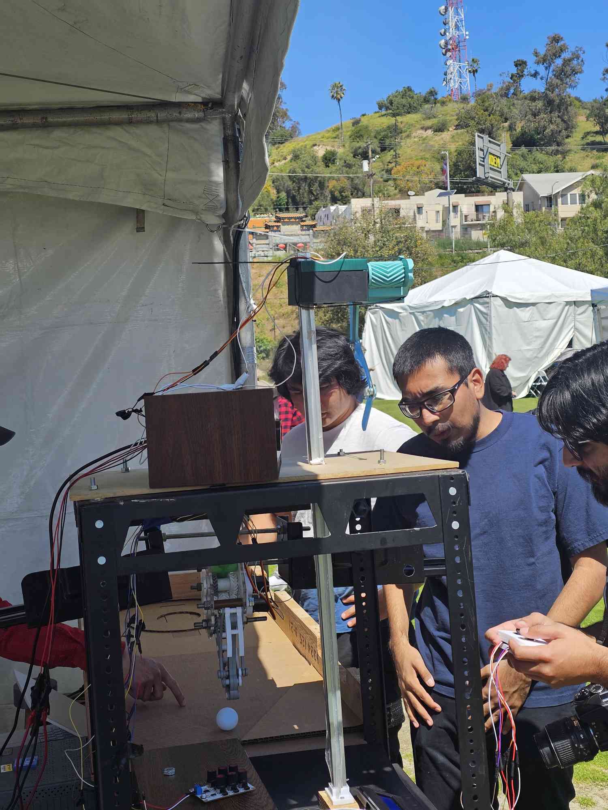
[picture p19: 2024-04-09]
events_photos/Spring_2024_Maker_Faire_Downtown_LA/20240406_113053.jpg

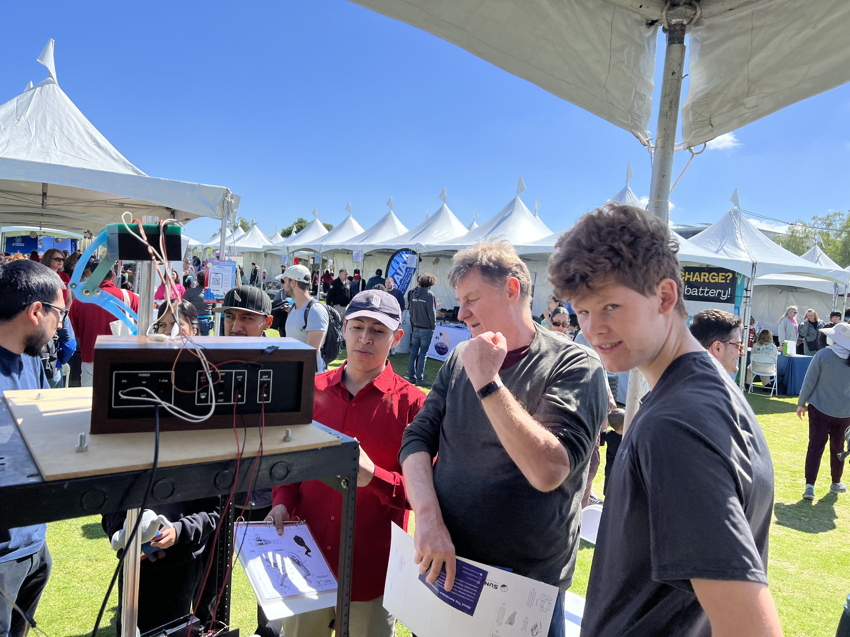
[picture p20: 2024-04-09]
events_photos/Spring_2024_Maker_Faire_Downtown_LA/IMG_6002.jpg

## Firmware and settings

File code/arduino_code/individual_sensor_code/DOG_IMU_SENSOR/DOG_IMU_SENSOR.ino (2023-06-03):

#include <Wire.h>
#include <LiquidCrystal.h>
#include <Adafruit_Sensor.h>
#include <Adafruit_BNO055.h>

//defining object of the Adafruit_BNO055 with a default address 0x55
Adafruit_BNO055 myIMU = Adafruit_BNO055(55, 0x28);
//Adafruit_BNO055 myIMU_bot = Adafruit_BNO055(56, 0x29);
//defining the Pins for the LED. If the LEDs are ON, then it means the Gyro or Accel is calibrated.
#define LED_Gyro 9
#define LED_Acc 10
//Define the variables:
bool calibrated = false;
uint8_t sys, gyro,accel, mg = 0; //intializeed system variables to 0
float thetaM; //angle of for the pitch from the accelerometer
float phiM;//angle for the roll from the accelerometer
float theta; //angle of for the pitch
float phi;//angle for the roll
float yaw; //angle of for the yaw
float dt;//time vectors
unsigned long millisOld; // old time being updated within dt

void setup() {
  //setting up serial monitor
  Serial.begin(9600);
  //Setting output pins for the two LEDS. When on, it will tell us if the sensor is calibrated
  pinMode(LED_Gyro, OUTPUT);
  pinMode(LED_Acc, OUTPUT);
  //turing on BNO055
  myIMU.begin();
  //myIMU_bot.begin();
  delay(1000);
  //dont use the crystal on chip, use the one on the board
  myIMU.setExtCrystalUse(true);
  //Start with the sensor calibration  
  while(calibrated == false){
    //get all and system calibrations
    myIMU.getCalibration(&sys, &gyro, &accel, &mg);
    //myIMU_bot.getCalibration(&sys2, &gyro2, &accel2, &mg2);
    if(gyro = 3){
      //If gyro sensor is fully calibrated then it will turn on an LED to indicate is calibrated.
      digitalWrite(LED_Gyro, HIGH);
    }
    if(accel == 3){
      //If Accelerometer sensor is fully calibrated then it will turn on an LED to indicate is calibrated.
      digitalWrite(LED_Acc, HIGH);
      //Since Calibrating the Accelerometer sensor takes longer and onces its fully calibrated, then it will get out from the while loop.
      calibrated = true;
      delay(3000);
    }
  }
  //Turn off the LEDS, so it doesn't consume any current.
  digitalWrite(LED_Gyro, LOW);
  digitalWrite(LED_Acc, LOW)
}

void loop() {
  //Accelerometer data: getting the data by vectors and using the period(dot) symbol to grab x, y or z data. These are raw data.
  imu::Vector<3> acc=myIMU.getVector(Adafruit_BNO055::VECTOR_ACCELEROMETER);
  //Accordinng to our calculatins our pitch angle is theta = tan(ax/az). Divede by 9.8 to normalize everything to 1g
  thetaM = atan2(acc.x() / 9.8, acc.z() / 9.8) / 2 / 3.1415 * 360;
  phiM = atan2(acc.y() / 9.8, acc.z() / 9.8) / 2 / 3.1415 * 360;
  //Gyroscope data: getting the data by vectors and using the period(dot) symbol to grpb x, y, and z data. These are raw data.
  imu::Vector<3> gyros=myIMU.getVector(Adafruit_BNO055::VECTOR_GYROSCOPE)
  //Since the raw data from gyro is deg/sec then we multiply dt, which is in sec, to the raw data to get degree. 
  dt=(millis()-millisOld)/1000.;
  millisOld=millis();
  //Pitch:
  theta = (theta - gyros.y() * dt) * .60 + thetaM * .40;
  //Roll:
  phi = (phi + gyros.x() * dt) * .60 + phiM * .40; 
  //Yaw:
  yaw = gyros.z();
  
  delay(50);
}

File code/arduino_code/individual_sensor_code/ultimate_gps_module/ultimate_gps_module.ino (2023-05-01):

#include <SoftwareSerial.h>
#include <Adafruit_GPS.h>

// Define RX/TX pins
#define RX_PIN 0
#define TX_PIN 1

// Initialize GPS module
SoftwareSerial GPSSerial(RX_PIN, TX_PIN);
Adafruit_GPS GPS(&GPSSerial);

// Set GPSECHO to 'false' to turn off echoing the GPS data to the Serial console
// Set to 'true' if you want to debug and listen to the raw GPS sentences
#define GPSECHO false

uint32_t timer = millis();

void setup()
{
  // Connect to the Serial Monitor
  Serial.begin(115200);
  while (!Serial);

  // Connect to the GPS module
  GPSSerial.begin(9600);
  
  // Wait for GPS module to initialize
  delay(1000);
  
  // Turn on RMC (recommended minimum) and GGA (fix data) including altitude
  GPS.sendCommand(PMTK_SET_NMEA_OUTPUT_RMCGGA);
  
  // Set the update rate
  GPS.sendCommand(PMTK_SET_NMEA_UPDATE_1HZ); // 1 Hz update rate
  
  // Request updates on antenna status, comment out to keep quiet
  GPS.sendCommand(PGCMD_ANTENNA);
  
  // Ask for firmware version
  GPSSerial.println(PMTK_Q_RELEASE);
}

void loop() // run over and over again
{
  // Read data from the GPS module
  char c = GPS.read();
  
  // If GPSECHO is true, print the GPS data to the Serial Monitor
  if (GPSECHO)
  {
    if (c) Serial.print(c);
  }
  
  // If a sentence is received, check the checksum and parse it
  if (GPS.newNMEAreceived())
  {
    if (!GPS.parse(GPS.lastNMEA()))
    {
      return;
    }
  }
  
  // Print out the current stats approximately every 2 seconds or so
  if (millis() - timer > 2000)
  {
    timer = millis(); // reset the timer
    
    Serial.print("\nTime: ");
    if (GPS.hour < 10) { Serial.print('0'); }
    Serial.print(GPS.hour, DEC); Serial.print(':');
    if (GPS.minute < 10) { Serial.print('0'); }
    Serial.print(GPS.minute, DEC); Serial.print(':');
    if (GPS.seconds < 10) { Serial.print('0'); }
    Serial.print(GPS.seconds, DEC); Serial.print('.');
    if (GPS.milliseconds < 10) { Serial.print("00"); }
    else if (GPS.milliseconds > 9 && GPS.milliseconds < 100) { Serial.print("0"); }
    Serial.println(GPS.milliseconds);
    
    Serial.print("Date: ");
    Serial.print(GPS.day, DEC); Serial.print('/');
    Serial.print(GPS.month, DEC); Serial.print("/20");
    Serial.println(GPS.year, DEC);
    
    Serial.print("Fix: "); Serial.print((int)GPS.fix);
    Serial.print(" quality: "); Serial.println((int)GPS.fixquality);
    if (GPS.fix)
    {
      Serial.print("Location: ");
      Serial.print(GPS.latitude, 4); Serial.print(GPS.lat);
      Serial.print(", ");
      Serial.print(GPS.longitude, 4); Serial.println(GPS.lon);
      Serial.print("Speed (knots): "); Serial.println(GPS.speed);
      Serial.print("Angle: "); Serial.println(GPS.angle);
      Serial.print("Altitude: "); Serial.println(GPS.altitude);
      Serial.println((int)GPS.satellites);
}}}

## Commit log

2023-02-28 added a camera file for openCV
2023-03-05 Added individual sensors code
2023-03-14 added lidar actual vs reference distance comparison
2023-05-01 cleaning directory
    [main_file.kicad_pcb, main_file.kicad_sch]
2023-05-21 adding more files from teams
    [00 - Table View.xlsx, big_and_small_servos_benefits.xlsx, check_box_list.xlsx]
2023-05-21 reorganizing the directory
    [0.25 ft.SLDPRT, 0.5 ft.SLDPRT, 0.75 ft.SLDPRT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]
2023-06-16 Added Gen0 servo mount
    [ServoMount_Dogv00.SLDPRT]
2023-06-23 Moving and updating files
    [Legv0_link1_Dogv00.SLDPRT, Legv0_link2_Dogv00.SLDPRT, MG995R Dogv00.SLDPRT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]
2023-06-23 updated units
    [Legv0_link2_Dogv00.SLDPRT, ServoMount_02_Dogv00.SLDPRT, ServoMount_Dogv00.SLDPRT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]
2023-06-24 modified stl file
    [ServoMount_Dogv00.SLDPRT, ServoMount_Dogv00.STL]
2023-07-07 split servo mount into two parts
    [ServoHolderTestbed01_side2.SLDPRT, ServoMount_Dogv00.SLDPRT]
2023-08-01 Servoholder v3
    [ServoHolderTestbed01_side2.3mf, ServoHolderTestbed01_side2.STL, ServoHolderTestbed03_side1.STL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]
2023-08-08 added 3d printer firmware (works and only have filament runout enable)
    [Configuration.h, Configuration_adv.h, esp32.csv]
2023-08-08 usable firmware
    [Configuration.h, Configuration_adv.h]
2023-08-15 New servo holder
    moved holes, resized dimensions. might need slight adjustments
    [ServoHolderTestBed04_side1.SLDPRT, ServoHolderTestBed04_side2.SLDPRT]
2023-08-15 servoholder gcode for printing
    [ServoHolderTestBed04_side1.STL, ServoHolderTestBed04_side2.STL, ServoMount04_side1.gcode.3mf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]
2023-08-29 added servo holder v4 gcode
2023-09-01 Made edits to cad and stl files for servo holder v4
    [ServoHolderTestBed04_side1.SLDPRT, ServoHolderTestBed04_side1.STL, ServoHolderTestBed04_side2.SLDPRT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]
2023-09-16 Create I2C_com_raspberry_pi_to_arduino
2023-09-16 Update I2C_com_raspberry_pi_to_arduino
2023-09-17 updated directory and added power script
2024-09-14 added inventory
    [Configuration.h, Configuration_adv.h, esp32.csv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]
